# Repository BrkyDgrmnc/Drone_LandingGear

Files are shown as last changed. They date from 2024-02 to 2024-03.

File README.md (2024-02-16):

# Drone_LandingPod <br/>

## Proje Bilgileri<br/>

  Bu proje, döner kanatlı insansız hava araçlarında kullanılmak üzere geliştirilmiş iniş takımının elektronik kartını içermektedir. Kart, iki adet 6V DC motoru kontrol etmek üzere tasarlanmıştır. Motorları sürmek için L9110 motor sürücü entegresi kullanılmıştır.<br/>
  
  
  <br/>

### Kart Özellikleri <br/>

- Kontrolcü **:** Arduino Pro Mini (ATmega328)<br/>
- Giriş Voltajı **:** 12V *(Not:Kontrolcü için harici 5V girişi gereklidir.)* <br/>
- Motor Çıkış Voltajı **:** 6V<br/>
- Çıkış Akımı **:** 800mA<br/>
- Anlık Tepe Akımı **:** 1500mA<br/>
<br/>

## PCB Görselleri <br/>

  
  <br/>
  


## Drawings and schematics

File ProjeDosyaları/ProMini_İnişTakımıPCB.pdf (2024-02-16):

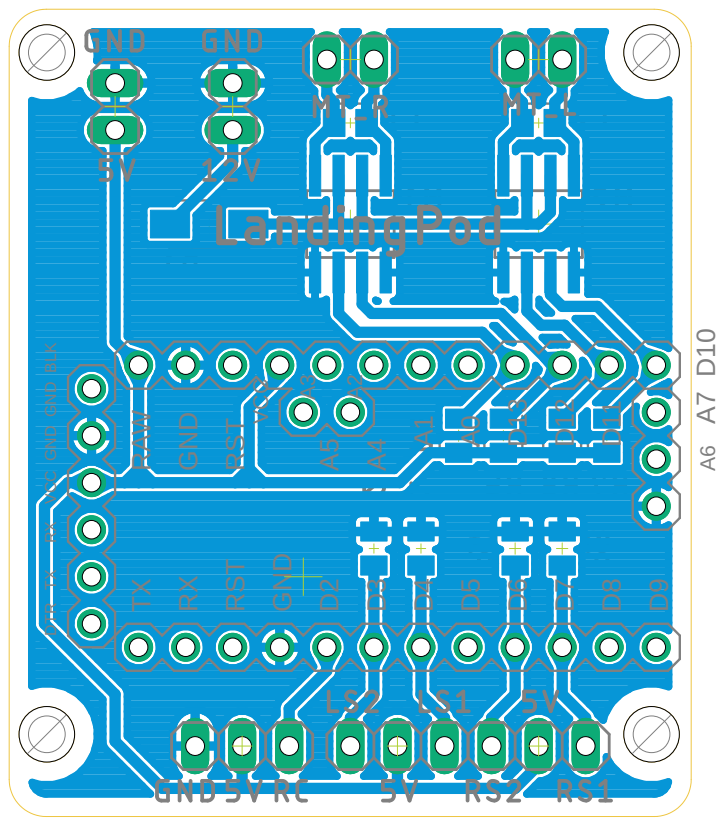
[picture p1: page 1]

RST GND D2 RXTX DTR TX RX VCC GND GND BLK D4 D5 D6 D7 D8 D9 D10 D11 D12 D13 A0A1 A2A3 VCC RST GND RAW D3 A6 A7 A5A4

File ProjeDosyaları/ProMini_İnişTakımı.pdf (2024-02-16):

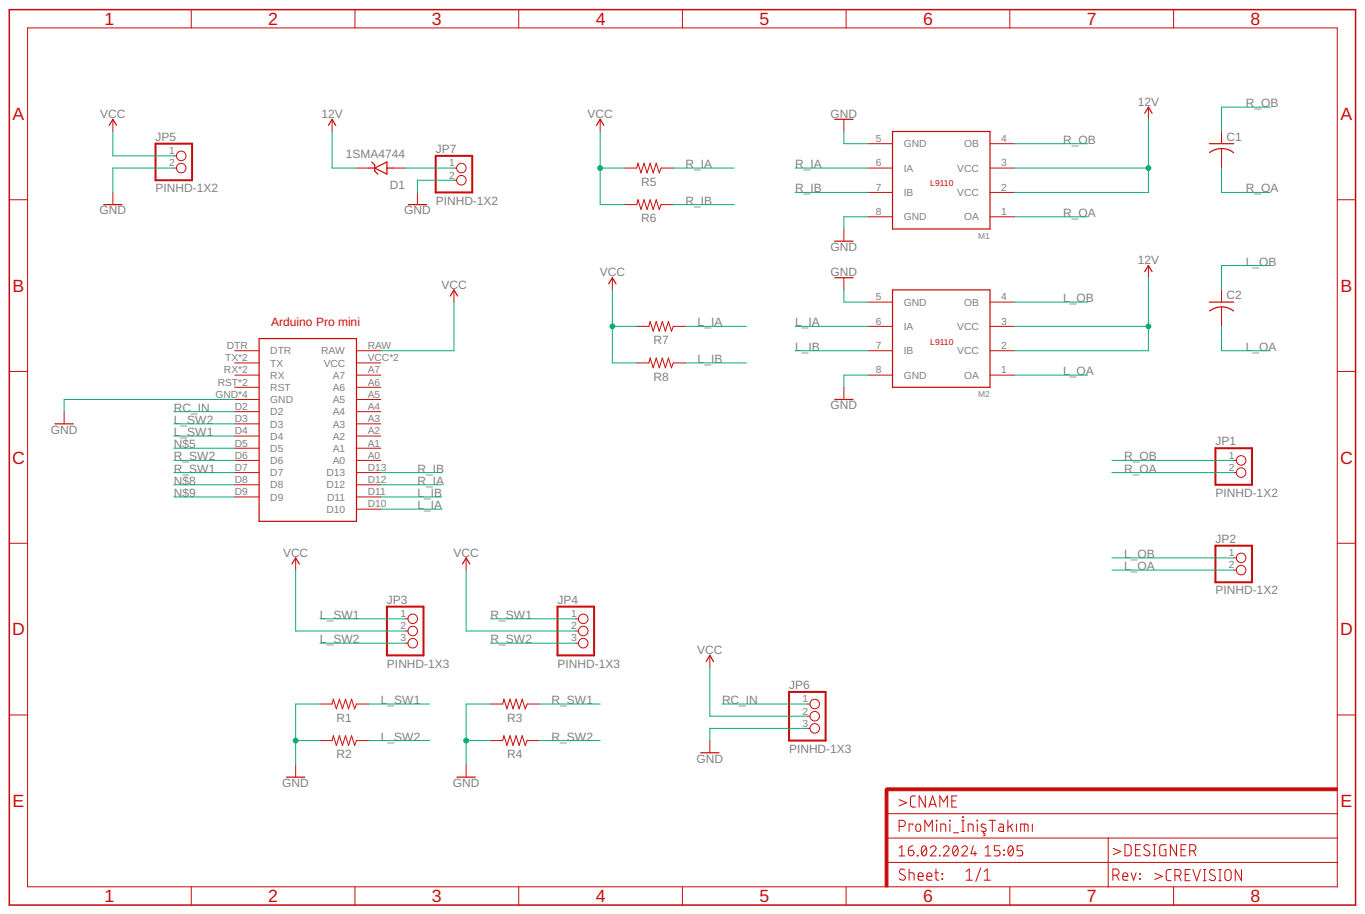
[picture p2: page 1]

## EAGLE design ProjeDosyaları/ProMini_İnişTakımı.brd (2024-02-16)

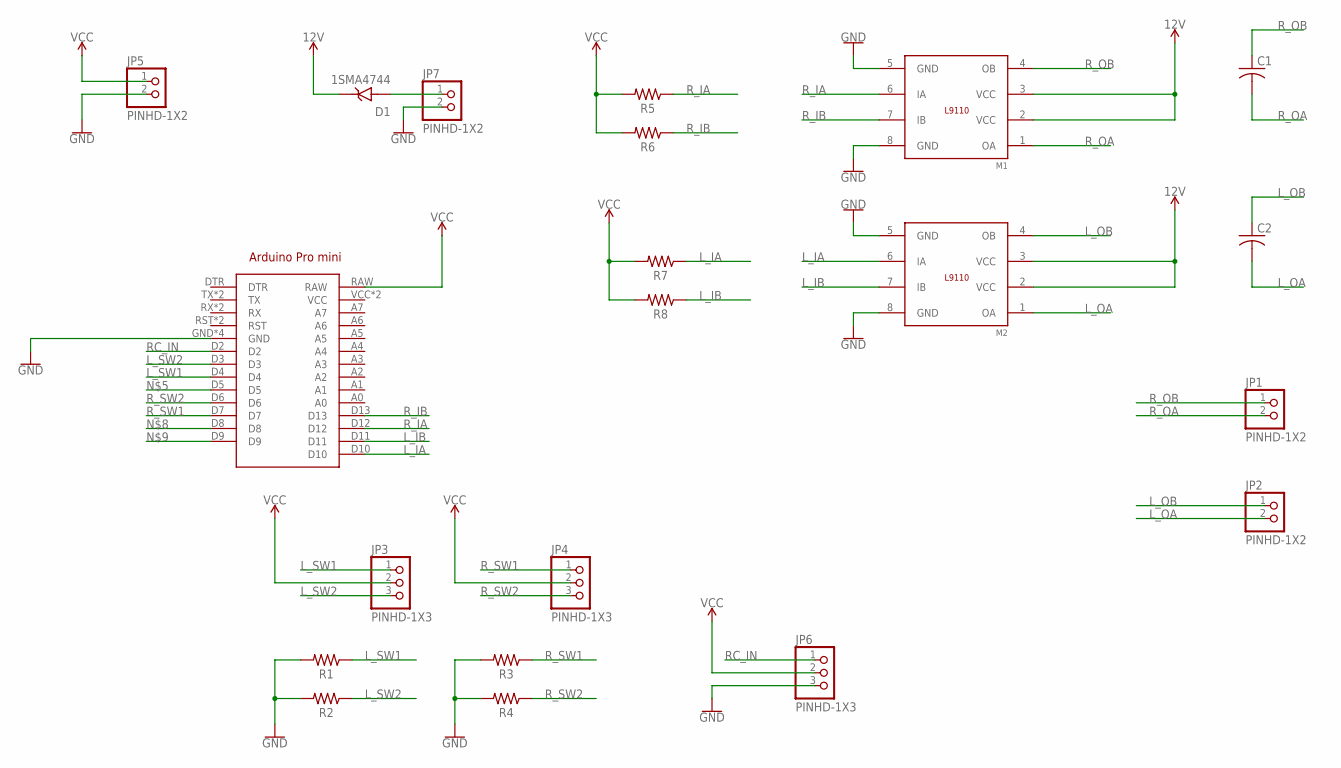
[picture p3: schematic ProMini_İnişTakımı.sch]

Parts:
ARDUINO1: ARDUINO_PRO_MINI
C1, C2: C-US_CHIP-0805(2012-METRIC); CAPC2012X110
D1: 1SMA4744; DIOM4325X250N
JP1, JP2, JP5, JP7: PINHD-1X2; 1X02
JP3, JP4, JP6: PINHD-1X3; 1X03
M1, M2: L9110; SO8P
R1, R2, R3, R4, R5, R6, R7, R8: R-US_CHIP-0805(2012-METRIC); RESC2012X65

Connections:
12V: D1.C (K), M1.2 (VCC), M1.3 (VCC), M2.2 (VCC), M2.3 (VCC)
GND: ARDUINO1.GND, ARDUINO1.GND@1 (GND), ARDUINO1.GND@2 (GND), ARDUINO1.GND@3 (GND), JP5.2, JP6.3, JP7.2, M1.5 (GND), M1.8 (GND), M2.5 (GND), M2.8 (GND), R1.2, R2.2, R3.2, R4.2
L_IA: ARDUINO1.D10, M2.6 (IA), R7.1
L_IB: ARDUINO1.D11, M2.7 (IB), R8.1
L_OA: C2.2, JP2.2, M2.1 (OA)
L_OB: C2.1, JP2.1, M2.4 (OB)
L_SW1: ARDUINO1.D4, JP3.1, R1.1
L_SW2: ARDUINO1.D3, JP3.3, R2.1
unnamed: D1.A, JP7.1
RC_IN: ARDUINO1.D2, JP6.1
R_IA: ARDUINO1.D12, M1.6 (IA), R5.1
R_IB: ARDUINO1.D13, M1.7 (IB), R6.1
R_OA: C1.2, JP1.2, M1.1 (OA)
R_OB: C1.1, JP1.1, M1.4 (OB)
R_SW1: ARDUINO1.D7, JP4.1, R3.1
R_SW2: ARDUINO1.D6, JP4.3, R4.1
VCC: ARDUINO1.RAW, ARDUINO1.VCC, ARDUINO1.VCC@1 (VCC), JP3.2, JP4.2, JP5.1, JP6.2, R5.2, R6.2, R7.2, R8.2

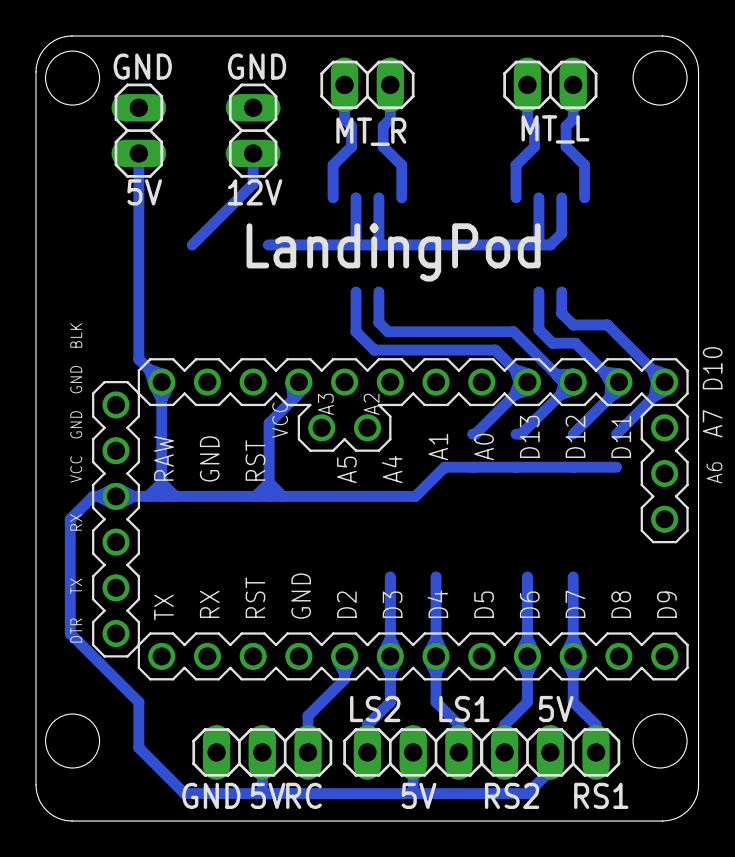
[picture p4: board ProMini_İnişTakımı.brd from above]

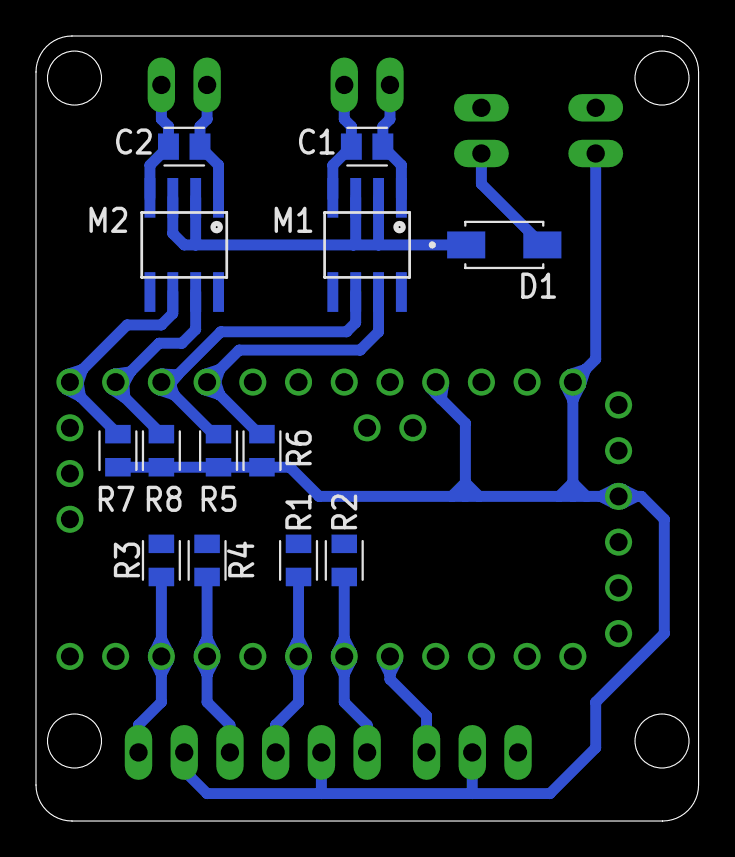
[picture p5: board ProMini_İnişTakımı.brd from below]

Board: 2 copper layers, 36.8 x 43.6 mm, 21 parts (13 on the bottom side), 17 nets.

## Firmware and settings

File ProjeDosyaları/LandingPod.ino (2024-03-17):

/*RC Input Pin*******************************/
#define RC_PIN          2                 /**/
/********************************************/

/*Motor Limit Switches***********************/
#define LSW_2           3                   //
#define LSW_1           4                   //
#define RSW_2           6                   //
#define RSW_1           7                   //
/********************************************/

/*Motor Direction Select Pins****************/
#define ROutA           12                  //
#define ROutB           13                  //
/*------------------------------------------*/
#define LOutA           10                  //
#define LOutB           11                  //
/********************************************/

#define TimeOutR        500
#define TimeOutL        500

unsigned int rcsignal = 1500;


unsigned long lastTimeR = 0;
bool j = true;
bool k = true;

unsigned long lastTimeL = 0;
bool i = true;
bool l = true;


void gearUp(int out_a , int out_b){
  digitalWrite(out_a, HIGH);
  digitalWrite(out_b, LOW);
}

void gearDown(int out_a , int out_b){
  digitalWrite(out_a, LOW);
  digitalWrite(out_b, HIGH);
}

void gearStop(int out_a , int out_b){
  digitalWrite(out_a, HIGH);
  digitalWrite(out_b, HIGH);
}

void GearLeft(){

  if(digitalRead(LSW_2) && rcsignal < 1400)
  {
    gearUp(LOutA , LOutB);
    i = true;
    k = true;
  }

  else if(digitalRead(LSW_1) && rcsignal > 1700)
  {
    gearDown(LOutA , LOutB);
    i = true;
    k = true;
  }

  else
  {
    if((!digitalRead(LSW_1) || !digitalRead(LSW_2)) && i)
    {
      lastTimeL = millis();
      i = false;
    } 
    if((millis() - lastTimeL) > TimeOutL && k)
    {  
      gearStop(LOutA , LOutB);
      k = false;
    } 
  }
}

void GearRight(){
    
  if(digitalRead(RSW_2) && rcsignal < 1400)
  {
    gearUp(ROutA , ROutB);
    j = true;
    l = true;
  }

  else if(digitalRead(RSW_1) && rcsignal > 1700)
  {
    gearDown(ROutA , ROutB);
    j = true;
    l = true;
  }
  
  else 
  {  
    if((!digitalRead(RSW_1) || !digitalRead(RSW_2)) && j )
    {
      lastTimeR = millis();
      j = false;
    }
    
    if((millis() - lastTimeR) > TimeOutR && l)
    {  
      gearStop(ROutA , ROutB);
      l = false;
    }
  }
}
  
void setup() {
  pinMode(RSW_1, INPUT_PULLUP);
  pinMode(RSW_2, INPUT_PULLUP);
  pinMode(LSW_1, INPUT_PULLUP);
  pinMode(LSW_2, INPUT_PULLUP);
  
  pinMode(RC_PIN, INPUT);      
  
  pinMode(ROutA, OUTPUT);
  pinMode(ROutB, OUTPUT);
  pinMode(LOutA, OUTPUT);
  pinMode(LOutB, OUTPUT);
  
  pinMode(LED_BUILTIN, OUTPUT);
  
  gearStop(ROutA , ROutB);
  gearStop(LOutA , LOutB);
  
  //Serial.begin(115200);
}

void loop() {
  
  rcsignal = pulseIn(RC_PIN, HIGH);
  //Serial.println(rcsignal);
  GearLeft();
  GearRight();
}

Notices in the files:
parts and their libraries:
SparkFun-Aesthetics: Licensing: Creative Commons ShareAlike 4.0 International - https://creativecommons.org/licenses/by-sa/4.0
